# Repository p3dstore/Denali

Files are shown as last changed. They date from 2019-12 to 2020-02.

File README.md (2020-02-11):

# Denali - Alpha 2
Project Denali is a CoreXY, Moving Bed, Medium Size, Bowden Drive, FDM Printer

This can be considered a fork of both the VORON1 and VORON2 Projects, and is a FORK of the V2 gantry, with some rethought parts, and with a brand new kinematic ballscrew driven bed leveling system, enclosure and electronics bay.

The main goal was to reduce complexity, while providing a fast reliable and ultimately simpler printer.

It is not in any way affiliated with VORON Design.

Our discord server can be found here: https://discord.gg/MzTR3zE

BOM/Sourcing Guide for a 250x250x200 Build can be found here: https://docs.google.com/spreadsheets/d/1O3eyVuQ6M4F03MJSDs4Z71_XyNjXL5HFTZr1jsaAtRc/edit?usp=sharing
Frame Calculator: https://docs.google.com/spreadsheets/d/17bdA1itJfFXpg5xXoUhM7PC9FFtjTBpXj1FjgBG_8xA/edit?usp=sharing

This printer features the following:
 - Fully Enclosed Design
 - Supported Build Volumes of ~200x200x200 to ~350x350x300
 - Single Bowden Fed Extruder (V6/Volcano and Mosquito Hotends Supported)
 - CoreXY Belt Path
 - Moving Bed with Tri-Stepper Leveling and Squaring
 - MGN9H Rail/Carriage Combo on all Axis
 - Dual Rail X Axis for Increased Stability
 - 0.9 Deg XY Steppers, 1.8 Deg Z and E Steppers
 - 6mm Belts on XY, 1204 Ballscrews on Z
 - Minimal Printed Parts
 - Designed to be Printed with ABS and/or Filled Nylons
- 32 bit controller standard, Dual Bigtree Tech SKRs + TMC2209 Drivers or Single FYSETC S6 + TMC2209 Drivers
 - 24V Power Standard
 - AC Mains Bed with Thermal Cutoff Fusing
 - Powered by Klipper: https://github.com/KevinOConnor/klipper/

This design is "backwards" compatible with the following VORON parts
 - Toolheads (Including the DD ones)
 - 1.6 Z Drive and Deck Plate
 - RAMPs controller (assuming you build your own configuration)
 - Mobius Extruder
 - LRS-200-12 PSU, and thus 12v power, assuming you make your own brackets and deck plate
 
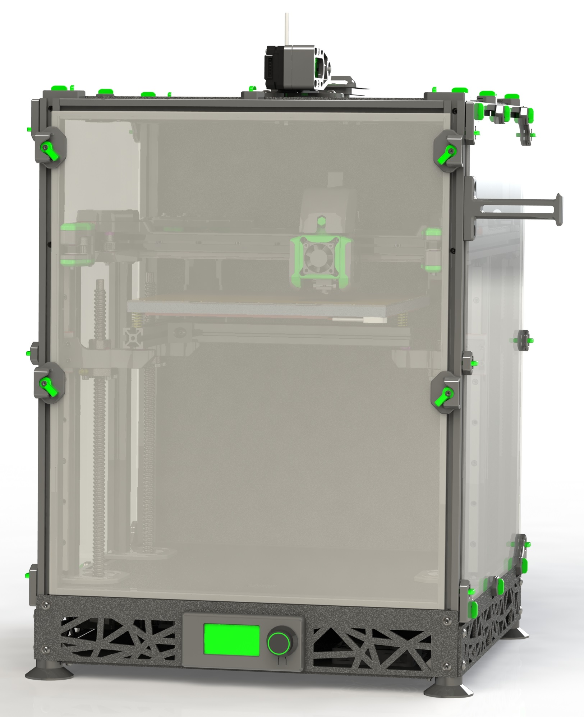
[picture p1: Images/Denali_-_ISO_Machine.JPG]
Image of Denali with Panels
 
 
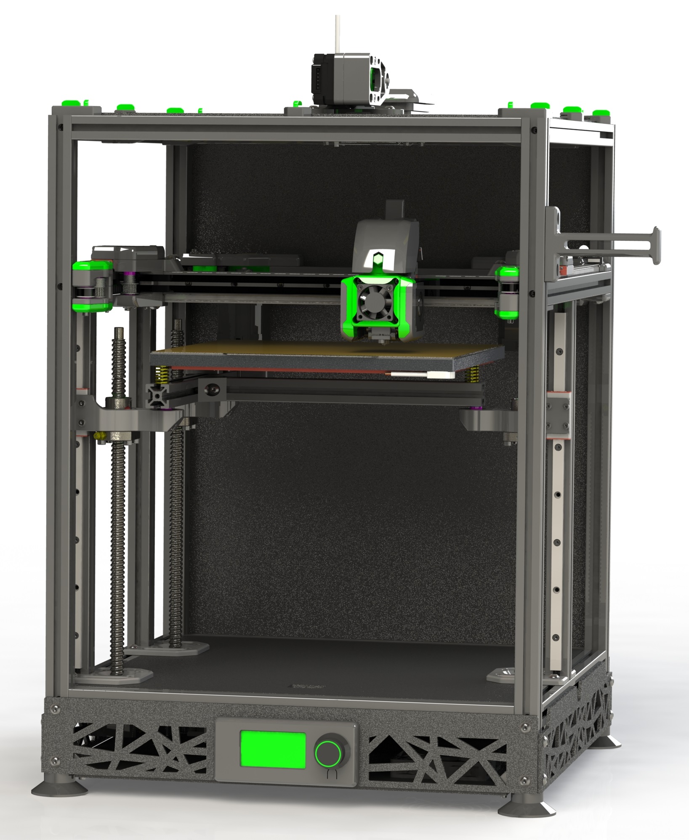
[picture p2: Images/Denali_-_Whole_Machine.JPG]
Image of Denali without Panels
 
  
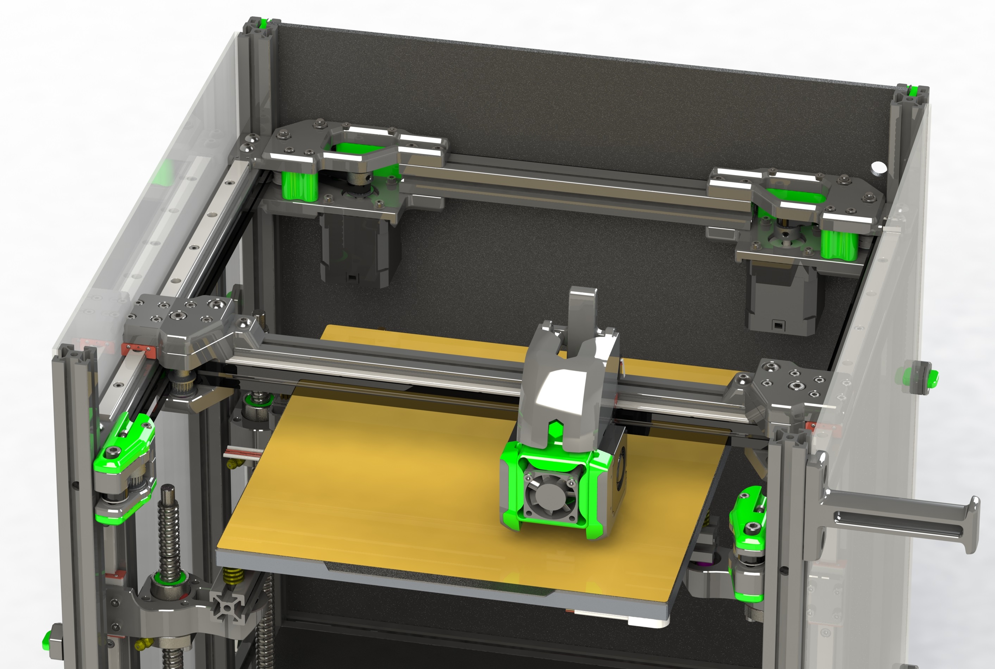
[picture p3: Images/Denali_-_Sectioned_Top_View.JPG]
Image of Denali Gantry
 
 
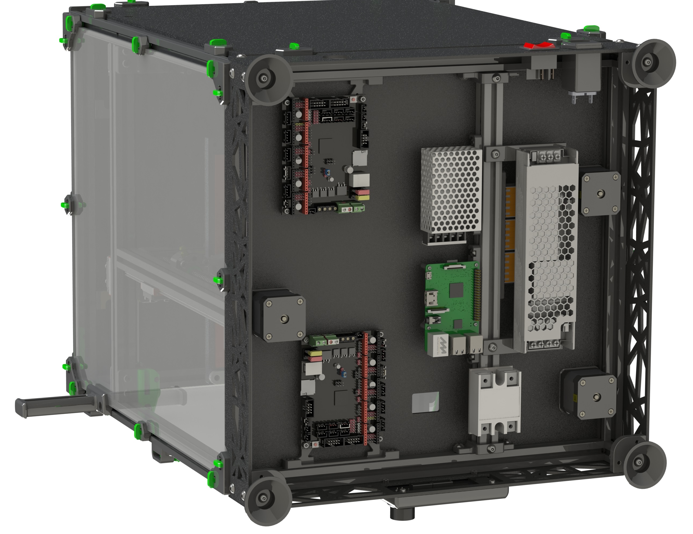
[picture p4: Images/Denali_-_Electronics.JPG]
Image of Denali Electrical Box


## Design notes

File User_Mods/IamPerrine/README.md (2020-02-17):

IamPerrine Denali Mods Directory

My Denali is a 350x350x200 build. I've gone a bit off script and here is all my mods. 

*Rear DC Electronics Mounts
-All the rear mounts have a panel spacer for 3mm ABS and 3mm of foam. A step file is inluded to mod to your panel spacing.
-Rear SKR 1.3 mounts with a 40mm fan mount to cool the drivers.
-Rear Pi4 Mount that clamps on to the heatsink of the pi. Using the Aliexpress heatsink from the Denali Sourcing Guide.
-Rear Wago 221 Mounts

*Magnet Quick Release Panel Mounts: Quick release magnet panel mounts developed with Cerulean from the Annex Discord. 

-Coming Soon: 
	*Nozzle Brush Mod
	*Printable Skirts

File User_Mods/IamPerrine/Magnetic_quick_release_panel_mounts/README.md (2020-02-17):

Magnet Panel Mounts with a pre insert magnet base. .stl files for my parts as well as .step files. 
Credit to Cerulean on the Annex Discord for getting the magent frame part made, and my panel mounts are based on their original mount. 

Magnets used: https://smile.amazon.com/gp/product/B077BWCC8D/ref=ppx_yo_dt_b_asin_title_o03_s00?ie=UTF8&psc=1

-The mounts are designed around 3mm thick foam and 3mm thick panels. It is recommended to print a test part to confirm it fits your panel before printing all of them. 
-Mounts are VHB taped to the panels. 
-Tolerances are for PLA, and magnets are a friction fit. If they fall out it doesn't matter since once it is on the panels the panel will stop the magnet from sliding out. 
-A panel rest or something for the panel to sit on at the bottom may be necessary to stop the whole panel from sliding down. If you superglue the magnet frame inserts into the 2020 extrusion, it may not be needed.

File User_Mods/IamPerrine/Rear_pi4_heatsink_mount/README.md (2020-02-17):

Pi4 Heatsink Rear Panel Mount
pi4 heatsink used: https://www.aliexpress.com/item/4000017705724.html Option Black With Fan
-Uses 4 m3x8 Socket Hex Head Screws to mount the holding tabs
-Panel insert is for 3mm panel and foam tape.

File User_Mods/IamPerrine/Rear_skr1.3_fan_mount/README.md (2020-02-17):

SKR 1.3 with 40mm Fan Rear Panel Mount

-Uses 4 m3x8 Socket Hex Head Screws to mount the skr to the bracket
-Uses 2 m3x16 Socket Hex head Screws to mount the 40x10mm fan to the bracket

Known issue: 

-Tolerances are tight when using the HE0 and HE1 headers with fan mounted on skr side of the mount tab.
-Mount the fan first if fan is mounted on skr side of mount tab.

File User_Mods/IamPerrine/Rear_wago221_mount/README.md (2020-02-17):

Wago 221 3 x 221-415 (5 conductor) Rear Panel Mount

-Wagos snap fit into bracket. This is modded from the stock wago mount to fit the same panel spacers as my other mods.

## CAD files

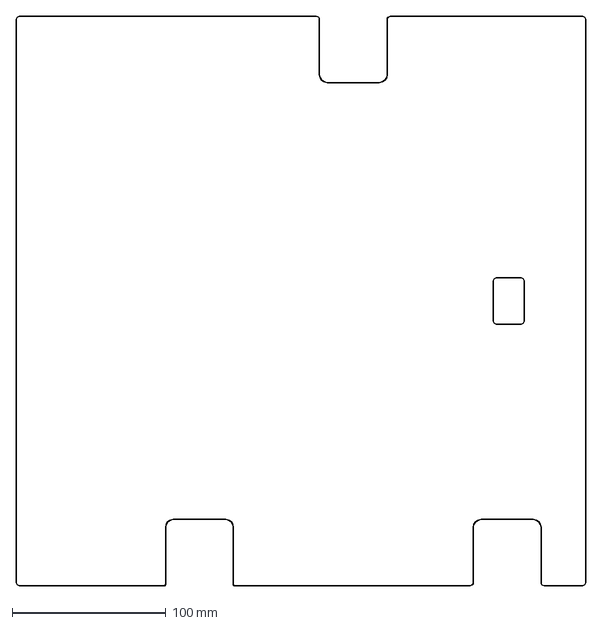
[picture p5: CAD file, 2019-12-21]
DXFs/Deck_Panel_250mm.DXF
370.0 x 370.0 mm

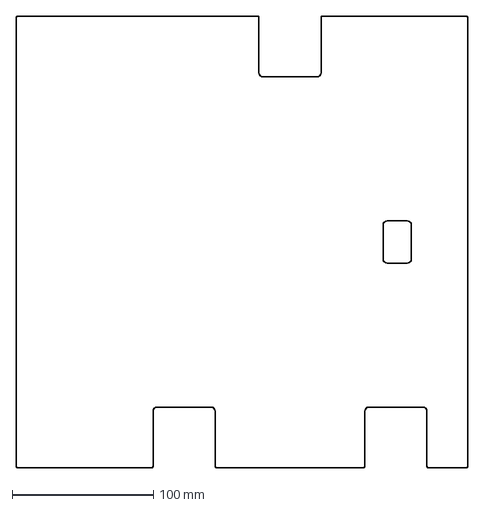
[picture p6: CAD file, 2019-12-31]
DXFs/Panels/Deck_Panel_200mm_Rev1.DXF
320.0 x 320.0 mm

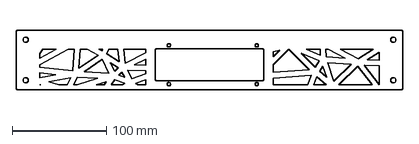
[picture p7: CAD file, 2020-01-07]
DXFs/Skirts/Front_Skirt_With_Screen_250mm_Rev1.DXF
410.0 x 63.0 mm

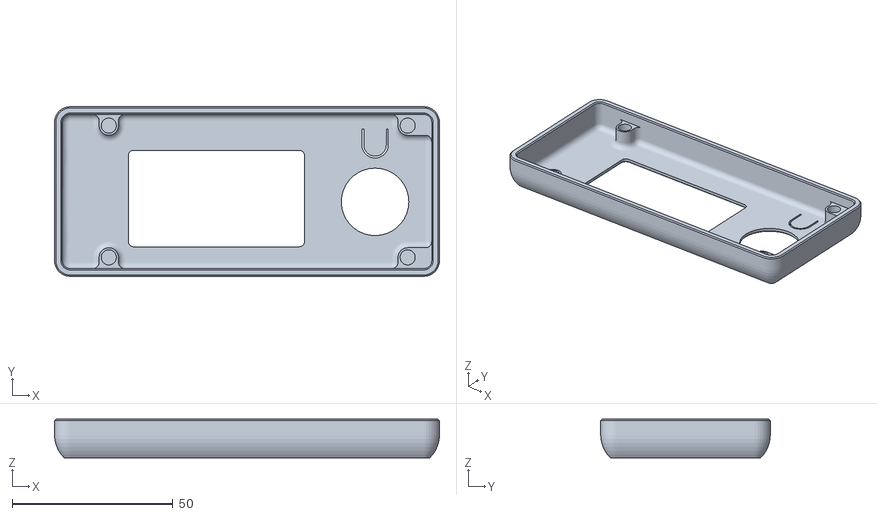
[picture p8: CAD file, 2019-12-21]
STLs/Display_Housing/fystec_mini_12864_housing_x1_Rev1.stl
119.8 x 52.8 x 12.0

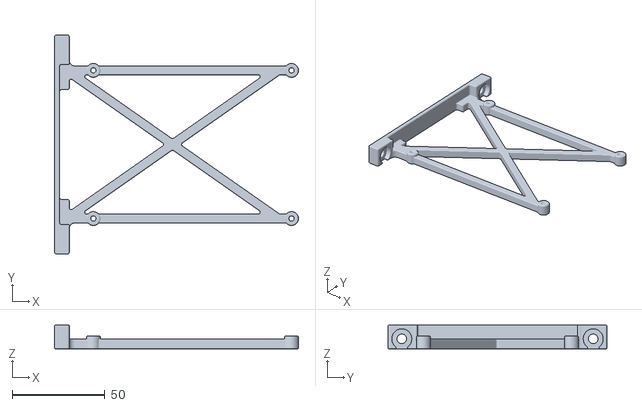
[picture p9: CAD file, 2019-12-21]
STLs/Electronics_Mounting/fysetc_s6_single_board_mounting_frame_x1_Rev1.STL
131.8 x 118.3 x 12.8

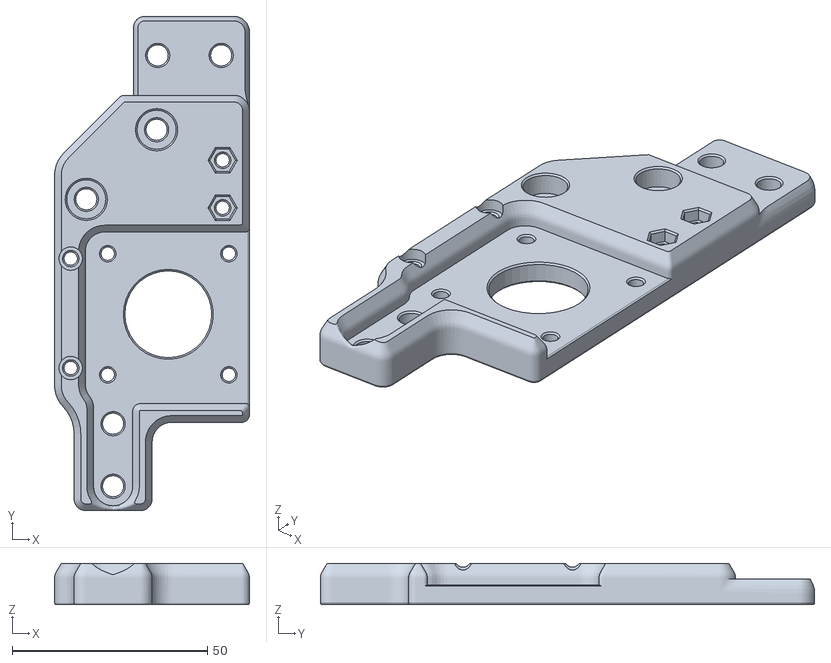
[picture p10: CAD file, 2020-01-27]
STLs/Gantry/AB_Drives/b_drive_frame_lower_x1_Rev2.stl
49.9 x 126.5 x 10.6

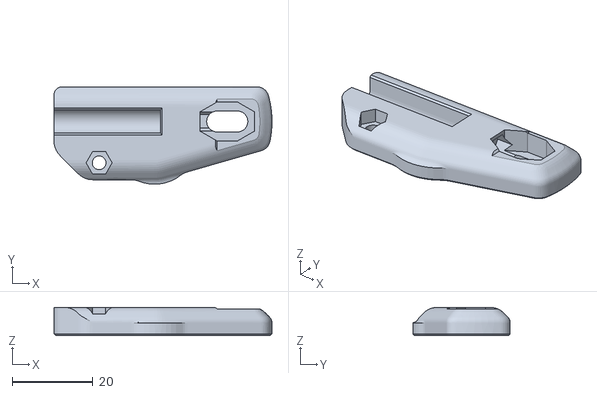
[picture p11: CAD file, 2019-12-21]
STLs/Gantry/Front_Idlers/[a]_front_idler_b_lower_cap_x1_Rev1.stl
54.1 x 24.2 x 7.00

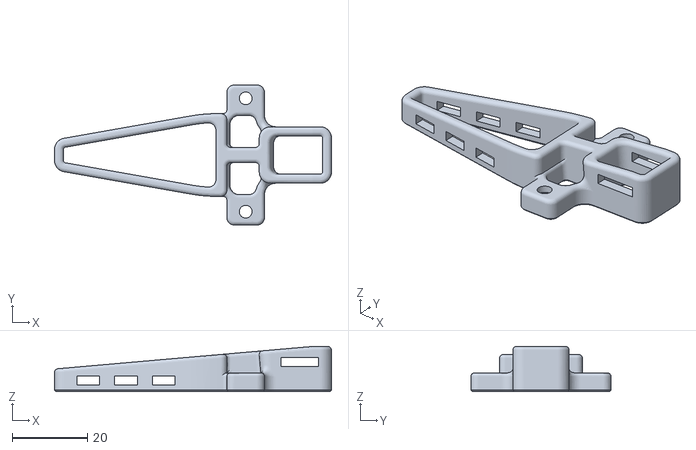
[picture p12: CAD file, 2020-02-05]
STLs/Gantry/X_Carriage_+_Toolhead/x_carriage_wire_support_Rev2.STL
73.6 x 37.2 x 12.0

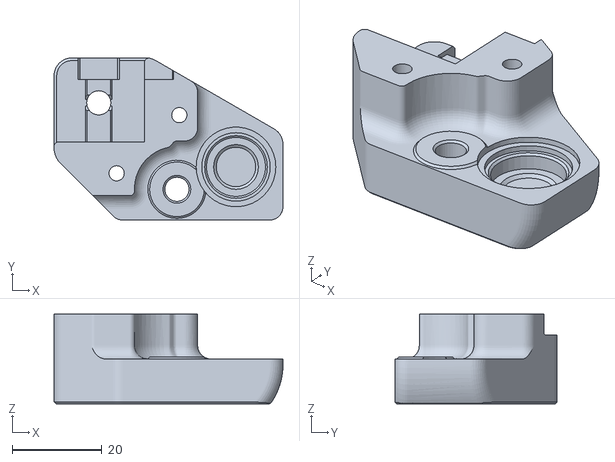
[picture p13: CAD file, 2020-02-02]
STLs/Gantry/XY_Joints/left_xy_joint_bottom_Rev2.stl
51.2 x 36.2 x 20.0

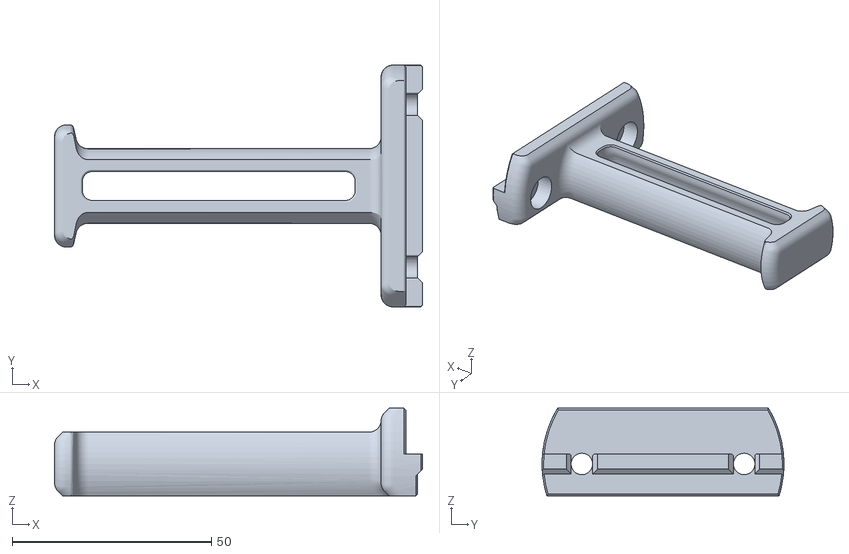
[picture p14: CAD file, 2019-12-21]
STLs/Misc/spool_holder_3mm_panels_x1_Rev1.stl
92.4 x 60.7 x 22.0

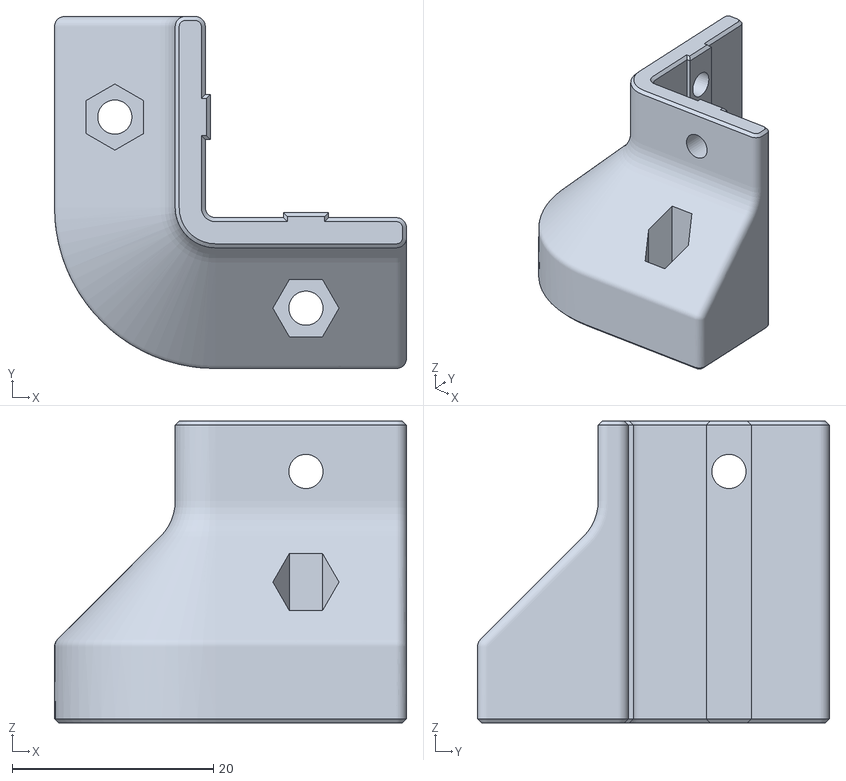
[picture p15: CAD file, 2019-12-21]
STLs/Panel_Mounting/bottom_panel_retaining_bracket_x4_Rev1.stl
35.0 x 35.0 x 30.0

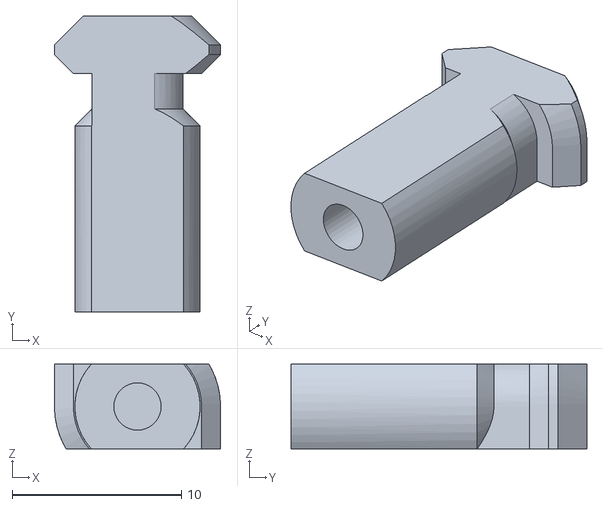
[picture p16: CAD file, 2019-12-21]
STLs/Panel_Mounting/Front_Panel_Quick_Release/[a]_latch_rhs_6mm_x2_Rev1.stl
9.82 x 17.5 x 5.00

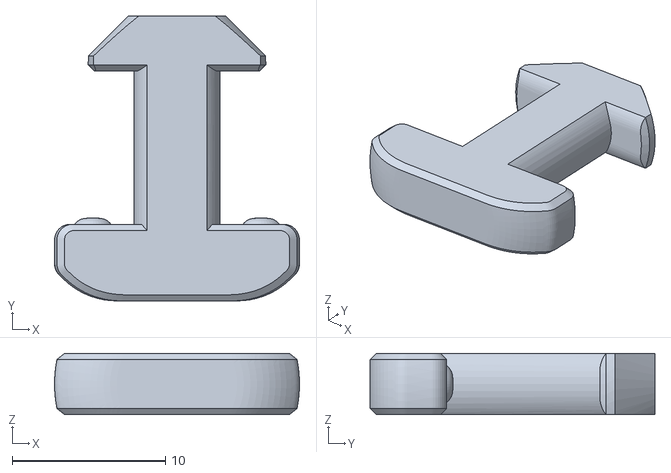
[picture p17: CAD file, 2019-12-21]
STLs/Panel_Mounting/Side_Top_and_Coroplast_Panel_Quick_Release/[a]_key_6mm_x34_Rev1.stl
16.0 x 18.6 x 4.00

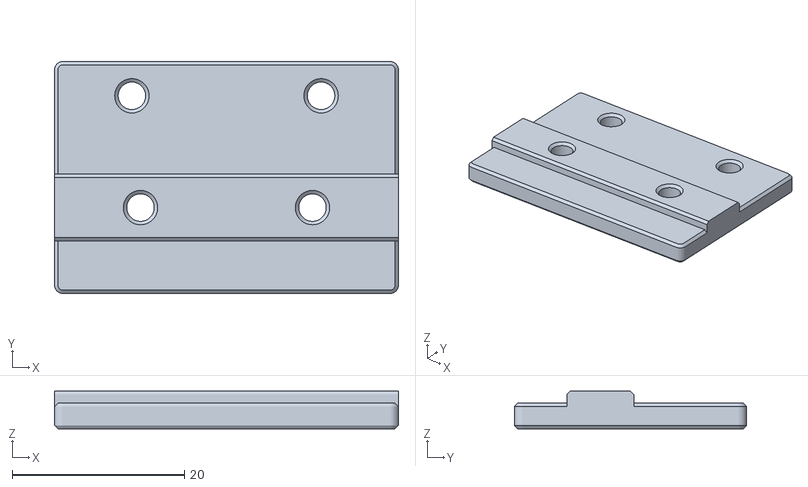
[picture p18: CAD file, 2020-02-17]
STLs/Z_Endstop/z_endstop_and_purgescrub_bucket_key_x1_rev1.STL
40.0 x 27.0 x 4.40

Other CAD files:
User_Mods/IamPerrine/Magnetic_quick_release_panel_mounts/Corner_Magnet_Frame_V3.STEP
User_Mods/IamPerrine/Rear_pi4_heatsink_mount/Panel Insert.stl
User_Mods/IamPerrine/Rear_skr1.3_fan_mount/Rear_SKR_Fan_Mount_v2.step
User_Mods/IamPerrine/Rear_wago221_mount/Panel Insert.stl
DXFs/Panels/Bottom_Panel_200mm_Rev1.DXF
DXFs/Panels/Bottom_Panel_250mm_Rev1.DXF
DXFs/Panels/Bottom_Panel_300mm_Rev1.DXF
DXFs/Panels/Bottom_Panel_350mm_Rev1.DXF
DXFs/Panels/Deck_Panel_250mm_Rev1.DXF
DXFs/Panels/Deck_Panel_300mm_Rev1.DXF
DXFs/Panels/Deck_Panel_350mm_Rev1.DXF
DXFs/Panels/Top_Panel_200mm_Rev1.DXF
DXFs/Panels/Top_Panel_250mm_Rev1.DXF
DXFs/Panels/Top_Panel_300mm_Rev1.DXF
DXFs/Panels/Top_Panel_350mm_Rev1.DXF
DXFs/Skirts/Back_Skirt_200mm_Rev1.DXF
DXFs/Skirts/Back_Skirt_250mm_Rev1.DXF
DXFs/Skirts/Back_Skirt_300mm_Rev1.DXF
DXFs/Skirts/Back_Skirt_350mm_Rev1.DXF
DXFs/Skirts/Front_Skirt_With_Screen_200mm_Rev1.DXF
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

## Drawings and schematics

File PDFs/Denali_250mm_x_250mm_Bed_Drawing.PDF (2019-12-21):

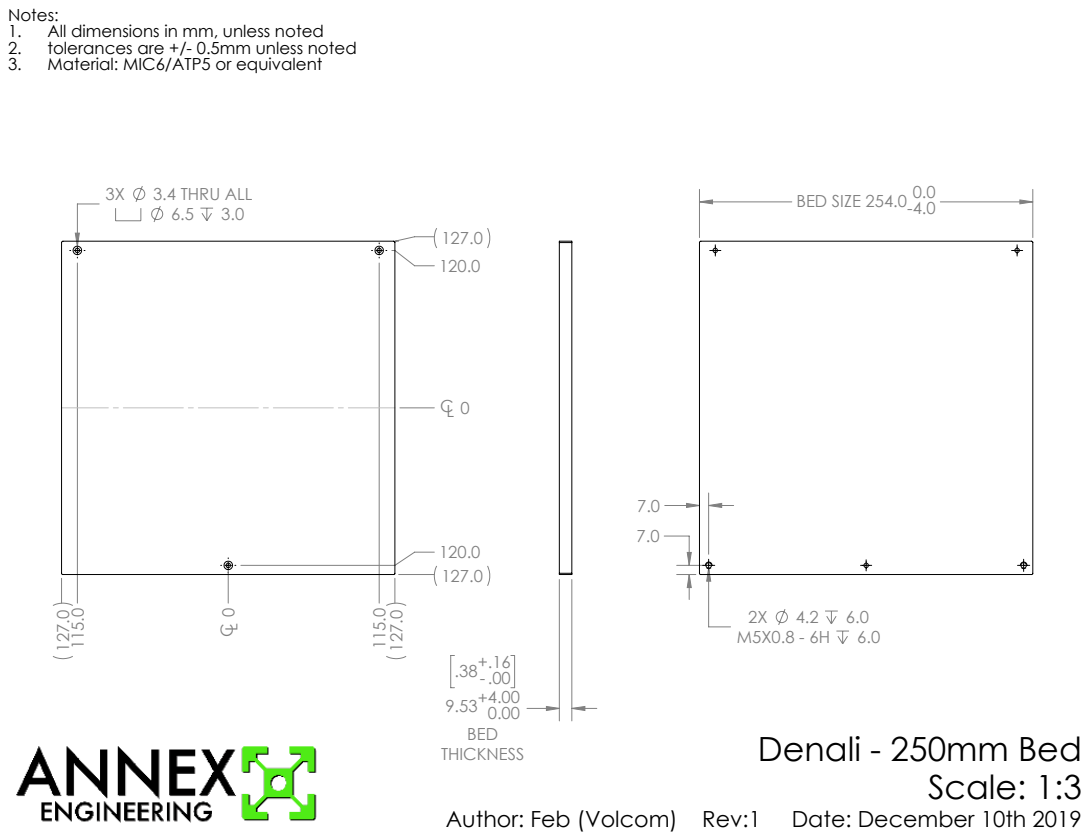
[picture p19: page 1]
3.4 THRU ALL; BED SIZE 254.0-; Denali - 250mm Bed Scale: 1:3

Notes:
1. All dimensions in mm, unless noted
2. tolerances are +/- 0.5mm unless noted
3. Material: MIC6/ATP5 or equivalent

Author: Feb (Volcom) Rev:1 Date: December 10th 2019

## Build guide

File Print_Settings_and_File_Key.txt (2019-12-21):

Primary Color: nothing at start of file name
Accent Color: [a]_ at start of file name
Quantity Required: _x# near end of file name
File Revision: _Rev# at end of file name

Approved FDM Materials: ABS, ABS+, or 3DXTech Carbon Nylon
Layer Height: 0.2mm
Extrusion Width: Forced 0.4mm
Infill Percentage: 40% minimum
Infill Type: Grid, Gyroid, Honeycomb, Triangle or Cubic
Wall Count: 4 minimum
Solid Top/Bottom Layers: 5 minimum

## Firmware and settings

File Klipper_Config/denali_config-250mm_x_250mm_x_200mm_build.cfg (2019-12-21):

# This file has been created by Feb, of Annex Engineering, for the Denali 3D Printer.
# Please change settings for your specific build or ensure you place your items in the same spots on the same MCU as I have.
# I've added as many options as I can think of for different displays as well as listed the available commands you can use via the terminal at the bottom of this configuration file.

#THIS CONFIG IS FOR A 250mm x 250mm x 200mm DENALI PRINTER ONLY
#PLEASE READ THE WHOLE CONFIG BEFORE ATTEMPTING TO DO ANYTHING
#CONNECTORS/PORTS ON THE CONTROLLERS ARE NOTED WITH COMMENTS FOR EACH LOCATION/INPUT/OUTPUT

#How do I upgrade to the latest software?
#The general way to upgrade is to ssh into the Raspberry Pi and run:
#cd ~/klipper
#git pull
#~/klipper/scripts/install-octopi.sh

#Then one can recompile and flash the micro-controller code. For example:
#make menuconfig
#make clean
#make
#sudo service klipper stop
#make flash FLASH_DEVICE=/dev/serial/by-id/usb-Klipper_Klipper_firmware_12345-if00
#sudo service klipper start

#However, it's often the case that only the host software changes. In this case, one can update and restart just the host software with:
#cd ~/klipper
#git pull
#sudo service klipper restart
#If after using this shortcut the software warns about needing to reflash the micro-controller or some other unusual error occurs, then follow the full upgrade steps outlined above. Note that the RESTART and FIRMWARE_RESTART g-code commands do not load new software - the above "sudo service klipper restart" and "make flash" commands are needed for a software change to take effect.


# use the following modifiers before the pin definition (ex: ^!ar99)
# ! 			invert the logic
# ^ 			activate 5v pullup (does not apply to all pins)
# mcu_name: 	use pins on additional MCU (ex: z:ar10)


# MCU XYE
[mcu] #You will need to set this definition manually following the instructions in the line below
#	obtain definition by "ls -l /dev/serial/by-id/" then unplug to verify
#	serial: /dev/serial/by-id/usb-Klipper_Klipper_firmware_12345-if00
restart_method: command

# MCU Z
[mcu z] #You will need to set this definition manually following the instructions in the line below
#	obtain definition by "ls -l /dev/serial/by-id/" then unplug to verify
#	serial: /dev/serial/by-id/usb-Klipper_Klipper_firmware_12345-if00
restart_method: command


#Printer Speeds and Accels
[printer]
kinematics: corexy
max_velocity: 300
max_accel: 2000
max_z_velocity: 25
max_z_accel: 300
square_corner_velocity: 5.0


# Stepper Configs
[stepper_x]
# connected to SKR XYE - X Stepper
step_pin: P2.8
dir_pin: P2.6
enable_pin: !P0.5
# 0.9deg - 160 steps per mm - 1/16 microstepping
step_distance: 0.00625
# connected to SKR XYE - Xmin Stepper
endstop_pin: !P1.29
position_min: 0
position_endstop: 250
position_max: 250
homing_speed: 100.0
second_homing_speed: 3.0
homing_retract_dist: 3.0
homing_positive_dir: true

[tmc2209 stepper_y]
uart_pin: P1.15
microsteps: 16
interpolate: false
run_current: 0.8 
sense_resistor: 0.110
stealthchop_threshold: 0

[stepper_y]
# connected to SKR XYE - Y Stepper
step_pin: P4.28
dir_pin: P2.1
enable_pin: !P0.5
# 0.9deg - 160 steps per mm - 1/16 microstepping
step_distance: 0.00625
# connected to SKR XYE - Ymin Stepper
endstop_pin: !P1.27
position_min: 0
position_endstop: 250
position_max: 250
homing_speed: 100.0
second_homing_speed: 3.0
homing_retract_dist: 3.0
homing_positive_dir: true
 
[tmc2209 stepper_y]
uart_pin: P1.17
microsteps: 16
interpolate: false
run_current: 0.8 
sense_resistor: 0.110
stealthchop_threshold: 0
 
[stepper_z]
# connected to SKR Z - X Stepper
step_pin: z:P2.8
dir_pin: z:P2.6
enable_pin: z:!P0.5
# 1.8deg - 800 steps per mm - 1/16 microstepping
step_distance: 0.00125
# connected to SKR Zmin Endstop
endstop_pin: z:P1.25

# offset for nozzle to bed off z switch
#	microswitch Pin Height off of the Bed
position_endstop: 0.000 #you'll need to measure this and set it, it controls your nozzle to bed offset
position_max: 180 #this is set here on purpose, your actual travel will vary based on spring compression holding the bed, adjust at your own risk
position_min: -5
homing_speed: 15.0
second_homing_speed: 5.0
homing_retract_dist: 10.0
homing_positive_dir: false
 
[tmc2209 stepper_z]
uart_pin: z:P1.15
microsteps: 16
interpolate: false
run_current: 0.7
sense_resistor: 0.110
stealthchop_threshold: 0
 
[stepper_z1]
# connected to SKR Z - Y Stepper
step_pin: z:P4.28
dir_pin: z:P2.1
enable_pin: z:!P0.5
# 1.8deg - 800 steps per mm - 1/16 microstepping
step_distance: 0.00125
 
[tmc2209 stepper_z1]
uart_pin: z:P1.17
microsteps: 16
interpolate: false
run_current: 0.7
sense_resistor: 0.110
stealthchop_threshold: 0
 
[stepper_z2]
# conected to SKR Z - E0 Stepper
step_pin: z:P0.10
dir_pin: z:P0.11
enable_pin: z:!P1.31
# 1.8deg - 800 steps per mm - 1/16 microstepping
step_distance: 0.00125

[tmc2209 stepper_z2]
uart_pin: z:P1.1
microsteps: 16
interpolate: false
run_current: 0.7
sense_resistor: 0.110
stealthchop_threshold: 0


# Force Move
#	used to force a single stepper to move.  not used once setup
#[force_move]
#enable_force_move: true

#	Enable Pause/Resume Functionality
[pause_resume]


# Probe
[probe]
# connected to SKR XYE - Zmax Endstop
endstop_pin: z:P1.24
x_offset: 0.0
y_offset: 25.0 # offset for inductive probe y direction off nozzle
z_offset: 0.00 # offset for inductive probe in z height, leave this set to zero
samples: 2
sample_retract_dist: 10.0
samples_result: average
samples_tolerance: 0.050
samples_tolerance_retries: 3
speed: 30


# Safe Z Home
# this allows you to home only z when the XY is already homed
[safe_z_home]
#home_xy_position: 1,1 # you'll need to change this to the home switch position, then uncomment the line
speed: 200.00
z_hop: 10.0
z_hop_speed: 20.0
move_to_previous: False

# Extruder0 - Rappel
[extruder]
# conected to SKR XYE - E0 Stepper
step_pin: P0.10
dir_pin: !P0.11
enable_pin: !P1.31
# 1.8deg - 558 steps per mm - 1/16 microstepping -  Rappel
step_distance: 0.001789

#0.4mm Nozzle
nozzle_diameter: 0.400
#pressure_advance: 0.35 #use a tuning tower to set your own values, these can be a starting value
#pressure_advance_smooth_time: 0.04 #use a tuning tower to set your own values, these can be a starting value
filament_diameter: 1.750	
max_extrude_only_distance: 1400.0
max_extrude_only_velocity: 120.0
max_extrude_only_accel: 15000.0
max_extrude_cross_section: 20000.0

# connected to SKR XYE - HE0 Heater
heater_pin: P2.7
max_power: 1.0

# connected to SKR XYE - TH0
sensor_type: ATC Semitec 104GT-2
sensor_pin: P0.24

#0.4mm Nozzle Settings
smooth_time: 3.0
max_power: 1.0

#Hotend PID Settings
control: pid
pid_Kp: 32.426 
pid_Ki: 1.743
pid_Kd: 150.782

min_extrude_temp: 0
min_temp: 0
max_temp: 300

[tmc2209 extruder]
uart_pin: P1.1
microsteps: 16
interpolate: false
run_current: 0.7
sense_resistor: 0.110
stealthchop_threshold: 0


 
# Heated Bed  
[heater_bed]
# connected to SKR XYE - FAN0
heater_pin: P2.3
# NTC 100K MGB18-104F39050L32 is for Kenovo thermistors
sensor_type: NTC 100K MGB18-104F39050L32
# connected to SKR XYE - HB Temp
sensor_pin: P0.23
smooth_time: 3.0

#Build Plate PID Settings
max_power: 0.60
control: pid
pid_Kp: 42.475 
pid_Ki: 1.395 
pid_Kd: 323.339
min_temp: 0
max_temp: 110


 
# Fans  
# Hotend Cooling Fan
[heater_fan my_nozzle_fan]
# connected to SKR XYE - FAN
pin: P2.3
max_power: 1.0
hardware_pwm: false
kick_start_time: 0.500
heater: extruder
heater_temp: 75.0
fan_speed: 1.00
 
# Print Cooling Fan
[fan]
# connected to SKR Z - FAN
pin: P2.3
max_power: 1.0
hardware_pwm: false
kick_start_time: 0.500


# Mesh Bed Settings
[bed_mesh]
speed: 200
horizontal_move_z: 12
min_point: 40,40
max_point: 260,260
probe_count: 5,5
fade_start: 1
fade_end: 0
split_delta_z: .025
move_check_distance: 5.0
mesh_pps: 2,2
algorithm: bicubic
bicubic_tension: 0.1
relative_reference_index: 12  # ^^^because were measuring the offset from the nozzle switch to the bed using the center of the bed, the equation to find the location = (probe point count)/2-1
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

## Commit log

2019-11-29 clean out fork
    [Bottom_Panel-Stock^3.DXF, Deck_Panel-Stock^3.DXF, [a]_belt_clip_x2.stl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]
2019-12-21 add DXFs, slicer config and bed PDF
    [Back_Skirt_250mm.DXF, Bottom_Panel_250mm.DXF, Deck_Panel_250mm.DXF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]
2019-12-21 add klipper config
    [denali_config-250mm_x_250mm_x_200mm_build.cfg]
2019-12-21 add STLs and edrawings
    [2020_electrical_beam_support_x2_Rev1.stl, [a]_front_frame_brace_x2_Rev1.stl, [a]_front_idler_a_lower_cap_x1_Rev1.stl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]
2019-12-21 update comments in SKR config, add preliminary experiemental S6 config
    [denali_bigtree_skr_1.3_config-250mm_x_250mm_x_200mm_build.cfg, denali_fysetc_s6_config-250mm_x_250mm_x_200mm_build.cfg, fysetc_s6_single_board_mounting_frame_x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]
2019-12-21 adjust abs unload temp on configs
    [denali_bigtree_skr_1.3_config-250mm_x_250mm_x_200mm_build.cfg]
2019-12-21 update macro name
    [denali_bigtree_skr_1.3_config-250mm_x_250mm_x_200mm_build.cfg, denali_fysetc_s6_config-250mm_x_250mm_x_200mm_build.cfg]
2019-12-21 refactor XY joint to 2 pieces
    [left_xy_joint_middle_Rev1.stl, left_xy_joint_top_Rev1.stl, left_xy_joint_top_Rev2.stl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]
2019-12-21 fix file corruption, source
    [left_xy_joint_top_Rev2.stl, left_xy_joint_top_Rev3.stl, right_xy_joint_top_Rev2.stl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]
2019-12-24 add heat set insert omron carriage
    add heat set insert omron carriage
    [x_carriage_frame_lhs_omron_heat_set_Inserts.STL, x_carriage_frame_rhs_omron_heat_set_Inserts.STL]
2019-12-31 add panel dxfs for standard configurations
    add panel dxfs for standard configurations
    [Back_Skirt_250mm_Rev1.DXF, Bottom_Panel_200mm_Rev1.DXF, Bottom_Panel_250mm_Rev1.DXF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]
2019-12-31 add rear skirt DXFs
    [Back_Skirt_200mm_Rev1.DXF, Back_Skirt_300mm_Rev1.DXF, Back_Skirt_350mm_Rev1.DXF]
2019-12-31 add side and front skirt dxfs
    add side and front skirt dxfs
    [Front_Skirt_With_Screen_200mm_Rev1.DXF, Front_Skirt_With_Screen_300mm_Rev1.DXF, Front_Skirt_With_Screen_350mm_Rev1.DXF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]
2020-01-07 fix fragmented dxf
    [Front_Skirt_With_Screen_200mm_Rev1.DXF, Front_Skirt_With_Screen_250mm_Rev1.DXF]
2020-01-08 updating config to reduce chance of moving out of bound "theoretically" at end of print
    code was originally borrow from fusion3d, an f400 machine, correcting error from 3 years ago
    [denali_bigtree_skr_1.3_config-250mm_x_250mm_x_200mm_build.cfg, denali_fysetc_s6_config-250mm_x_250mm_x_200mm_build.cfg]
2020-01-09 Alpha 2 cad files
    Alpha 2 cad files
2020-01-12 update klipper config to match new mesh changes
    update klipper config to match new mesh changes
    [denali_bigtree_skr_1.3_config-250mm_x_250mm_x_200mm_build.cfg, denali_fysetc_s6_config-250mm_x_250mm_x_200mm_build.cfg]
2020-01-22 allow AB drive to use long ballspring t-nuts
    allow AB drive to use long ballspring t-nuts
    [a_drive_frame_lower_x1_Rev1.stl, a_drive_frame_lower_x1_Rev2.stl, a_drive_frame_upper_x1_Rev1.stl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]
2020-01-27 re-orient bottom AB drives
    [a_drive_frame_lower_x1_Rev2.stl, b_drive_frame_lower_x1_Rev2.stl]
2020-02-02 add ballscrew nut removal tool
    add ballscrew nut removal tool
2020-02-02 clearance bottom xyjoint caps by 2mm
    clearance bottom xyjoint caps by 2mm
    [left_xy_joint_bottom_Rev1.stl, left_xy_joint_bottom_Rev2.stl, right_xy_joint_bottom_Rev1.stl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]
2020-02-05 modify x_carriage wire support for access to ascender tensioning screw
    [x_carriage_wire_support_Rev1.stl, x_carriage_wire_support_Rev2.STL]
2020-02-11 correct uart pin on e0, z mcu
    correct uart pin on e0, z mcu
    [denali_bigtree_skr_1.3_config-250mm_x_250mm_x_200mm_build.cfg]
2020-02-11 correct other wrong uart address
    [denali_bigtree_skr_1.3_config-250mm_x_250mm_x_200mm_build.cfg]
2020-02-12 correct print cooling fan pin
    wasnt on z mcu
    [denali_bigtree_skr_1.3_config-250mm_x_250mm_x_200mm_build.cfg]
2020-02-12 Update denali_bigtree_skr_1.3_config-250mm_x_250mm_x_200mm_build.cfg
    delete un-used macros, re-enable turn off of bed heater and motors at end of print
    [denali_bigtree_skr_1.3_config-250mm_x_250mm_x_200mm_build.cfg]
2020-02-12 Update denali_fysetc_s6_config-250mm_x_250mm_x_200mm_build.cfg
    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
    [denali_fysetc_s6_config-250mm_x_250mm_x_200mm_build.cfg]
2020-02-14 Added user mod directory and loaded my mods
    [PI Mount Body.stl, PI Mount Tab x3.stl, PI Mount big tab.stl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]
2020-02-14 Fixed my wago mount.
    [wago221_mount x2.stl]
2020-02-17 Added magnet panel mounts
    [Corner Magnet Panel V1.stl, Corner_Magnet_Frame_V3.STEP, Corner_Magnet_Frame_V4.STL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]
2020-02-17 beta1 files
    [keyed_back_panel_x1_Rev1.stl, microswitch_pulley_housing_mg2t_20t_x1_Rev1.stl, z_endstop_and_purgescrub_bucket_key_x1_rev1.STL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]
